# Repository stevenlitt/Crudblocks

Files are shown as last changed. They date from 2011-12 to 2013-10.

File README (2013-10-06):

Crudlabs Crudblocks

Arduino-based Modular Robotic Drum Controller

For a basic explanation of this project, please check out the Introduction to Crudblocks page on the wiki: https://github.com/stevenlitt/Crudblocks/wiki/Introduction-to-Crudblocks

All code, instructions, images, and other information and content 
provided strictly for non-commercial use.

Crudlabs + Crudblocks � Crudlabs 2012

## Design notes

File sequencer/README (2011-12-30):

Contains:

Arduino code (.pde)

Parts lists (.xls Excel spreadsheets)

3d printer files (.stl, .gcode, and .skp models designed in Google Sketchup)

PCB files (.sch, .brd, and gerbers)

where necessary for each sequencer module.

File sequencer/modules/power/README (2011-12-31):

Info on the power module and the recommended power supply coming early 2012.

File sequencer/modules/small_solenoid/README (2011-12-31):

This module uses the same Arduino code and PCBs as the "big_solenoid" module.

The parts list can also be found online as a Google Spreadsheet:

https://docs.google.com/spreadsheet/ccc?key=0AqVR8pqyuewQdG43TWpadEtsWEc4RVlPZjJQaXdpSFE

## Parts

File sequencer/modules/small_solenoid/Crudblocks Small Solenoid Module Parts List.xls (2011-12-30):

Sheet: Arduino on Breadboard
COMPONENT | QUANTITY | WHERE TO BUY | PART NUMBER | VENDOR PART NUMBER | ADDITIONAL COMMENTS | PRICE/UNIT | LINK
Multipurpose PC Board with 417 Holes | 1 | Radio Shack | 276-150 | 276-150 |  | 2.19 | http://www.radioshack.com/product/index.jsp?productId=2102845
Atmega328 with Arduino Bootloader | 1 | Sparkfun | DEV-10524 | DEV-10524 |  | 5.5 | http://www.sparkfun.com/products/10524
Violet LED | 1 | Sparkfun | COM-09851 | COM-09851 | in pack of 25 for $7.95 | 0.32 | http://www.sparkfun.com/products/9851
Standoff - Nylon (3/4", 4-40) | 4 | Sparkfun | PRT-10315 | PRT-10315 |  | 0.5 | http://www.sparkfun.com/products/10315
DIP Sockets Solder Tail - 28-Pin 0.3" | 1 | Sparkfun | PRT-07942 | PRT-07942 |  | 1.5 | http://www.sparkfun.com/products/7942
4-40 3/8" Screw | 8 | Mcmaster | 90279A108 | 90279A108 | in pack of 100 for $4.21. | 0.04 | http://www.mcmaster.com/#90279a108/=fb40lr
Mini Reset Switch | 1 | Mouser | B3F-1002 | 653-B3F-1002 |  | 0.24 | http://www.mouser.com/ProductDetail/Omron-Electronics/B3F-1002/
16MHz Clock Crystal | 1 | Mouser | ATS16A-E | 774-ATS16A-E |  | 0.54 | http://www.mouser.com/ProductDetail/CTS-Electronic-Components/ATS16A-E/
20pF Capacitor | 2 | Mouser | 140-100N2-200J-RC | 140-100N2-200J-RC | for clock | 0.08 | http://www.mouser.com/ProductDetail/Xicon/140-100N2-200J-RC/
10uF Capacitor | 1 | Sparkfun | COM-00523 | COM-00523 | between power and ground | 0.45 | http://www.sparkfun.com/products/523
10KOhm Resistor | 1 | Sparkfun | COM-08374 | COM-08374 | for reset switch | 0.25 | http://www.sparkfun.com/products/8374
330 Ohm Resistor | 1 | Sparkfun | COM-08377 | COM-08377 | for LED | 0.25 | http://www.sparkfun.com/products/8377
DIN5 Thru Hole Jack | 2 | Mouser | 161-0504-E | 161-0504-E |  | 0.98 | http://www.mouser.com/ProductDetail/Kobiconn/161-0504-E/?qs=xCMk%252bIHWTZMcaA%2fBF%2fgbrg%3d%3d

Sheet: Unique Parts
COMPONENT | QUANTITY | WHERE TO BUY | PART NUMBER | VENDOR PART NUMBER | ADDITIONAL COMMENTS | PRICE/UNIT | LINK
Solenoid | 1 | Lady Ada | 421 | 421 |  | 9.95 | http://www.adafruit.com/products/412
Screw Terminals 2.54mm Pitch (2-Pin) | 1 | Sparkfun | PRT-10571 | PRT-10571 |  | 0.75 | http://www.sparkfun.com/products/10571
4A Solid State Relay | 1 | Mouser | AQZ102 | 769-AQZ102 |  | 10.42 | http://www.mouser.com/ProductDetail/Panasonic-Electric-Works/AQZ102/
10KOhm Resistor | 1 | Sparkfun | COM-08374 | COM-08374 | for special command listener | 0.25 | http://www.sparkfun.com/products/8374
Mini Reset Switch | 1 | Mouser | B3F-1002 | 653-B3F-1002 | for special command listener | 0.24 | http://www.mouser.com/ProductDetail/Omron-Electronics/B3F-1002/
4-40 3/8" Screw | 8 | Mcmaster | 90279A108 | 90279A108 | in pack of 100 for $4.21. | 0.04 | http://www.mcmaster.com/#90279a108/=fb40lr

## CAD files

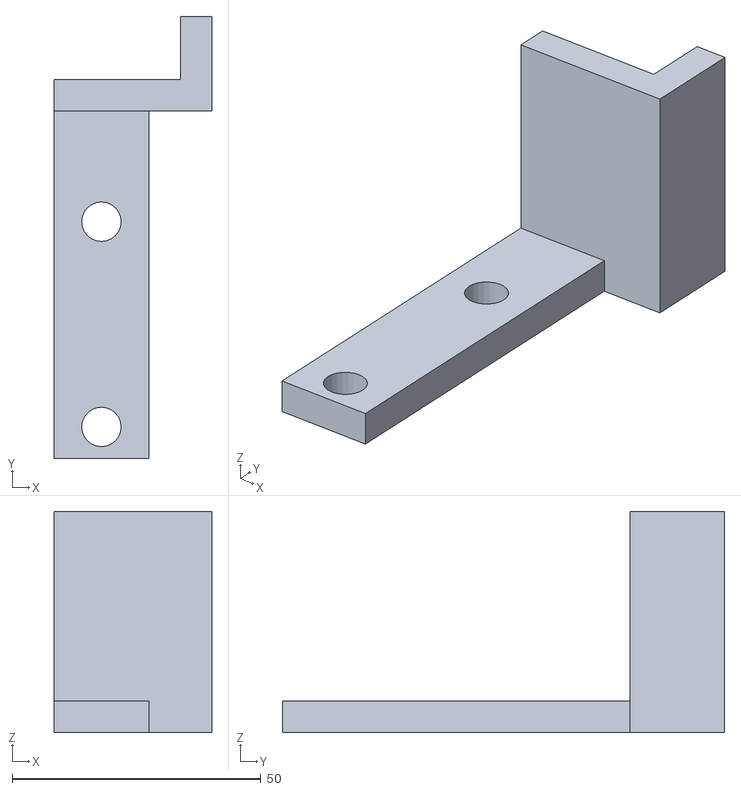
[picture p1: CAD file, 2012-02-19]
sequencer/modules/big_solenoid/makerbot/object_holder.stl
31.8 x 88.9 x 44.5

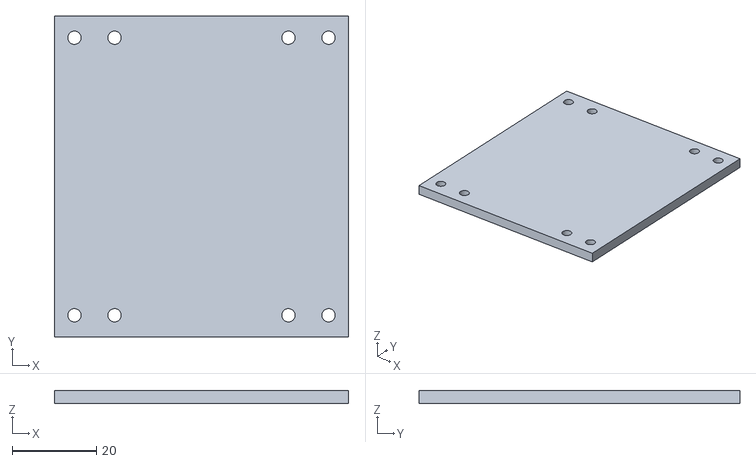
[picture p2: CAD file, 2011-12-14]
sequencer/modules/double_solenoid/makerbot/double_solenoid_electronics_connector_top.stl
69.8 x 76.2 x 3.18

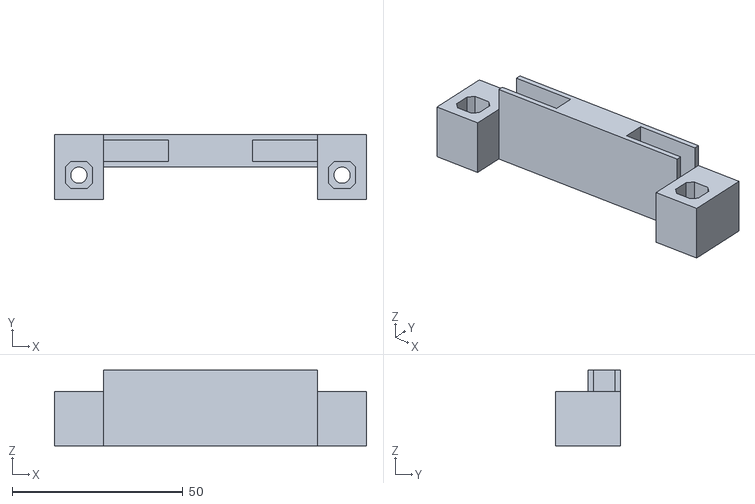
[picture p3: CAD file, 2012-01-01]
sequencer/modules/eight_step_sequencer/makerbot/double_standoff_joiner_with_magnet.stl
91.3 x 19.1 x 22.2

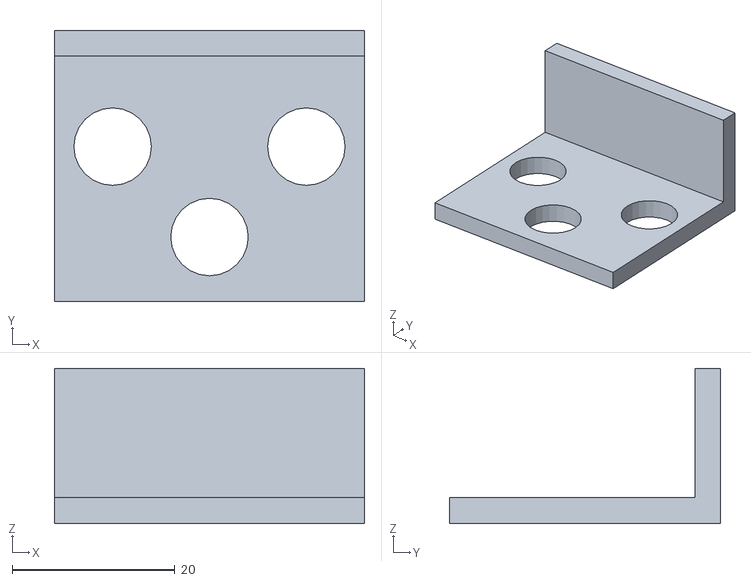
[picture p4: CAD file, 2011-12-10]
sequencer/modules/power/makerbot/power_module.stl
38.1 x 33.3 x 19.1

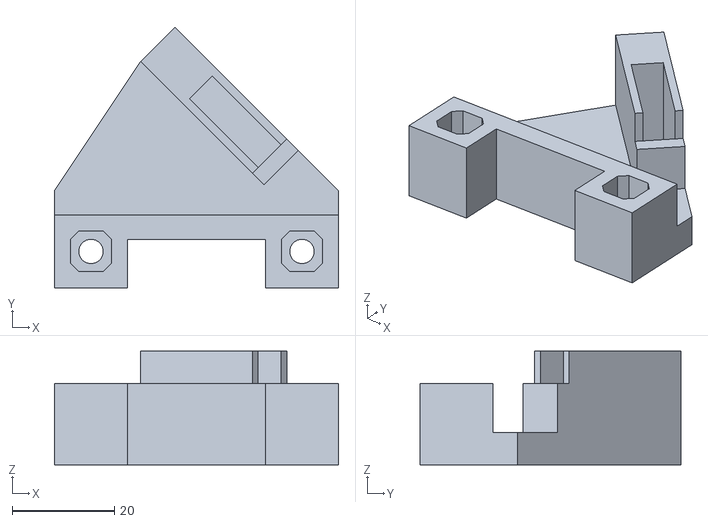
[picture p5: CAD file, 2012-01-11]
sequencer/modules/seven_seg_with_rot_encoder/makerbot/angled_standoff_joiner_with_magnet.stl
55.6 x 51.0 x 22.2

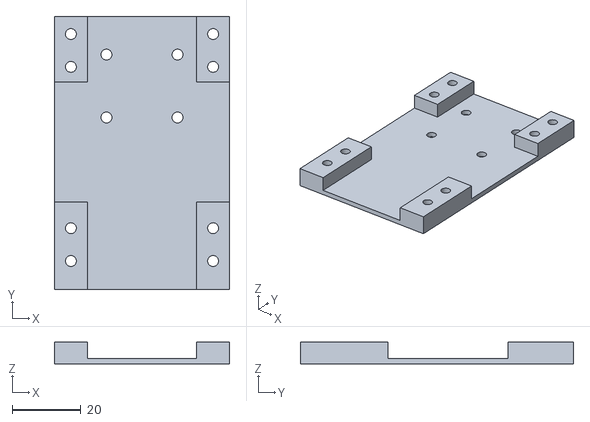
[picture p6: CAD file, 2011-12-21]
sequencer/modules/small_solenoid/makerbot/small_solenoid_electronics_connector.stl
50.8 x 79.4 x 6.35

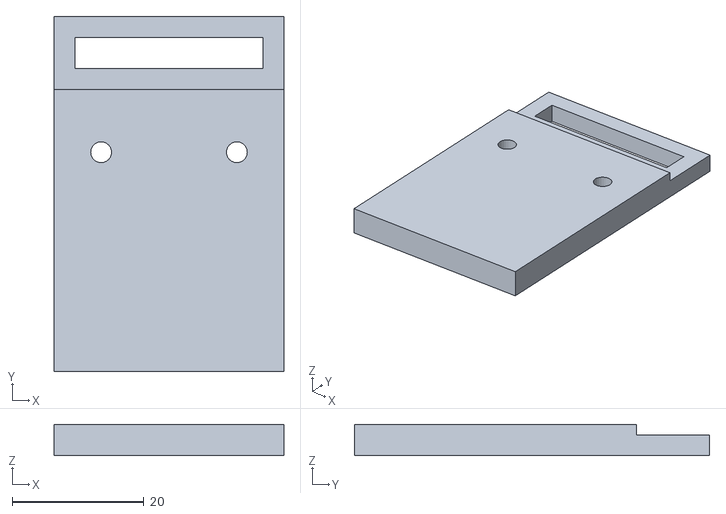
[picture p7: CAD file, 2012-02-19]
sequencer/modules/big_solenoid/makerbot/harness_longer.stl
34.9 x 54.0 x 4.76

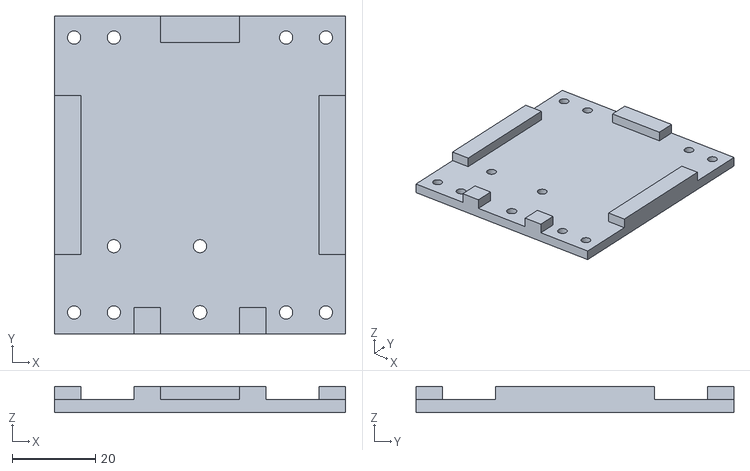
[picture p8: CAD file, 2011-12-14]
sequencer/modules/double_solenoid/makerbot/double_solenoid_electronics_connector_bottom.stl
69.8 x 76.2 x 6.35

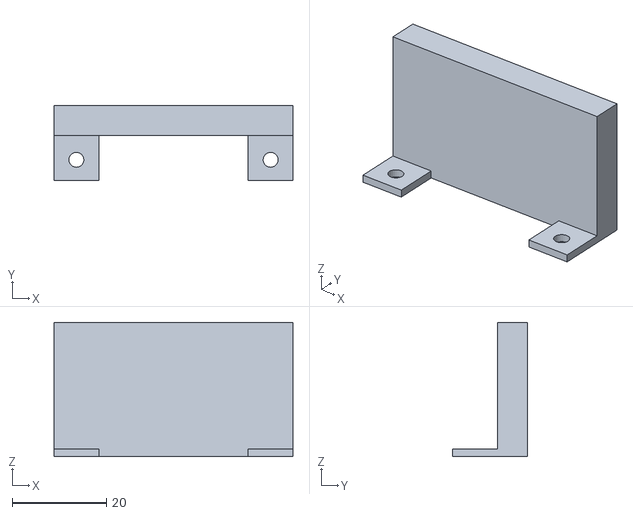
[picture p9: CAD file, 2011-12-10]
sequencer/modules/seven_seg_with_rot_encoder/makerbot/pcb_stand.stl
50.8 x 15.9 x 28.6

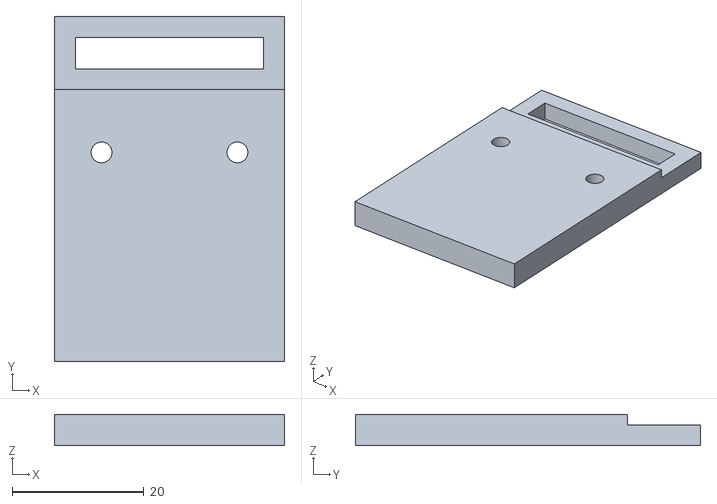
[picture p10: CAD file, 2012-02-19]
sequencer/modules/big_solenoid/makerbot/harness2.stl
34.9 x 52.4 x 4.76

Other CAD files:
sequencer/modules/big_solenoid/makerbot/harness2.skp
sequencer/modules/big_solenoid/makerbot/harness2~.skp
sequencer/modules/big_solenoid/makerbot/object_holder.skp
sequencer/modules/big_solenoid/makerbot/object_holder~.skp
sequencer/modules/double_solenoid/makerbot/double_solenoid_electronics_connector_bottom.skp
sequencer/modules/double_solenoid/makerbot/double_solenoid_electronics_connector_bottom~.skp
sequencer/modules/double_solenoid/makerbot/double_solenoid_electronics_connector_top.skp
sequencer/modules/eight_step_sequencer/makerbot/double_standoff_joiner_with_magnet.skp
sequencer/modules/eight_step_sequencer/makerbot/standoff_joiner_with_magnet.skp
sequencer/modules/eight_step_sequencer/makerbot/standoff_joiner_with_magnet~.skp
sequencer/modules/power/makerbot/power_module.skp
sequencer/modules/seven_seg_with_rot_encoder/makerbot/angled_standoff_joiner_with_magnet.skp
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

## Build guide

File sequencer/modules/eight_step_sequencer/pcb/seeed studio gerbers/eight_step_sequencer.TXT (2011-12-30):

%
M48
M72
T01C0.0240
T02C0.0276
T03C0.0300
T04C0.0320
T05C0.0400
T06C0.0520
T07C0.1250
%
T01
X8601Y14101
X17101Y16601
X21101Y19601
X26101Y20601
X26601Y21101
X35101Y16101
X35601Y10601
X31101Y7601
X27601Y4601
T02
X20101Y17601
X19101Y17601
X23101Y19601
X24101Y19601
X26101Y19601
X27101Y19601
T03
X29617Y17601
X31585Y17601
X31085Y10101
X29117Y10101
X26085Y10101
X24117Y10101
X21085Y10101
X19117Y10101
X16085Y10101
X14117Y10101
X11085Y10101
X9117Y10101
X6085Y10101
X4117Y10101
X4117Y5601
X6085Y5601
X9117Y5601
X11085Y5601
X14117Y5601
X16085Y5601
X19117Y5601
X21085Y5601
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

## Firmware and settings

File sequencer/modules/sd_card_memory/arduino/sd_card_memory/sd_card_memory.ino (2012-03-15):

/*----------------------------------------------------------------------
 
Crudlabs + Crudblocks Big Solenoid Module

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
 ----------------------------------------------------------------------*/
 

/*----------------------------------------------------------------------

   Sparkfun COM-09482 type 4 digit 7 segment display pinout diagram

                            16 15 14 13 12 11 10 9
                            ======================
                            |                    |
                            |8.  8.  :  8.  8.   |
                            |                    |
                            ======================
                            1  2  3  4  5  6  7  8


                  
                  AAAAAAA  AAAAAAA        AAAAAAA  AAAAAAA  
                  F     B  F     B        F     B  F     B  
                  F     B  F     B  COL   F     B  F     B  
                  F     B  F     B        F     B  F     B  
                  GGGGGGG  GGGGGGG        GGGGGGG  GGGGGGG  
                  E     C  E     C        E     C  E     C  
                  E     C  E     C  COL   E     C  E     C  
                  E     C  E     C        E     C  E     C  
                  DDDDDDD  DDDDDDD        DDDDDDD  DDDDDDD  



                          pin 1  =  digit 1 control
                          pin 2  =  digit 2 control
                          pin 6  =  digit 3 control
                          pin 8  =  digit 4 control
                          pin 3  =  LED D
                          pin 5  =  LED E
                          pin 11 =  LED F
                          pin 13 =  LED C
                          pin 14 =  LED A
                          pin 15 =  LED G
                          pin 16 =  LED B
  
----------------------------------------------------------------------*/

 
#include <SD.h>

#define channelSetterByte B11110001
#define next8Byte B11110011
#define switchChannelByte B11110010
#define setNumChannelsByte B11110100
#define setTempoByte B11110110
#define nextStepByte B11111001

#define BEGINLOADBYTE B11000001
#define LOADSTEPBYTE B11000010
#define ENDLOADBYTE B11000011
#define ENDCHANNELLOADBYTE B11000100

#define STARTSAVEBYTE B11000101
#define ENDSAVEBYTE B11000110
#define SAVEBITBYTE B11000111
#define SAVENEXTBYTE B11001000

//encoder stuff to delete after testing
#define SAVE_MODE 0
#define LOAD_MODE 1
#define numModes 2

int chipSelectPin = 2;
int ledLoadPin = 8;
int ledSavePin = 9;
int configPin = 7;

//encoder
int dpInEncoderA = A2;
int dpInEncoderB = A3;

//shift regs
int shiftOutLatchPin = 3;  //ST_CP of 74HC595
int shiftOutDataPin = 4;   //DS of 74HC595
int shiftOutClockPin = 5;  //SH_CP of 74HC595

//encoder
int encoderButtonPin = 6;
boolean encoderButtonValue = LOW;
boolean lastEncoderButtonValue = LOW;
int sevenSegDisplayMode = LOAD_MODE;
boolean showingWord = false;
unsigned long showingWordStartTime;
String wordToShow = "";
int encoderSubCount = 0;
int newEncoderPosition = 0;
int oldEncoderPosition = 0;

//7 seg
int digit1Address = 1;
int digit2Address = 1 << 1;
int digit3Address = 1 << 2;
int digit4Address = 1 << 3;

int currentPattern = 1;  //maybe need to change this name... ?  its the current pattern num displayed on the 7seg.... not the one playing on the sequencers

boolean lastConfigPinVal = LOW;

byte threeBytes[3] = {0, 0, 0};

boolean doMain = false;

unsigned long turnOnTime;
unsigned long preMainInterval = 3000;

File myFile;

String savedPattern = "";
String loadedPattern = "";

boolean sdInited = false;

boolean saving = false;
byte numChannelsSaved = 0;


void setup()
{
  Serial.begin(115200);
  pinMode(ledLoadPin, OUTPUT);  
  pinMode(ledSavePin, OUTPUT);
  
  pinMode(configPin, INPUT);
  
  //apparently we need to do this for the sd reader  
  pinMode(chipSelectPin, OUTPUT);  
  pinMode(10, OUTPUT);
  
  //for encoder
  pinMode(dpInEncoderA, INPUT);
  pinMode(dpInEncoderB, INPUT);  
  pinMode(encoderButtonPin,  INPUT);
  
  //for shiftregs
  pinMode(shiftOutLatchPin, OUTPUT);
  pinMode(shiftOutClockPin, OUTPUT);
  pinMode(shiftOutDataPin, OUTPUT);

  digitalWrite(dpInEncoderA, HIGH);
  digitalWrite(dpInEncoderB, HIGH);
  
  initSD();

  if(sdInited == true) initMode();
  
  turnOnTime = millis(); 
}

void loop() 
{
  goMain();  
}

void goMain() 
{
  checkConfigPin();  
  listenForSerial();
  readEncoder(); 
  checkEncoderSwitch();  
  draw7Seg();  
}

//CONFIG CONFIG CONFIG CONFIG CONFIG CONFIG CONFIG CONFIG CONFIG CONFIG CONFIG CONFIG CONFIG CONFIG CONFIG CONFIG CONFIG CONFIG CONFIG CONFIG CONFIG 
//CONFIG CONFIG CONFIG CONFIG CONFIG CONFIG CONFIG CONFIG CONFIG CONFIG CONFIG CONFIG CONFIG CONFIG CONFIG CONFIG CONFIG CONFIG CONFIG CONFIG CONFIG CONFIG 
//CONFIG CONFIG CONFIG CONFIG CONFIG CONFIG CONFIG CONFIG CONFIG CONFIG CONFIG CONFIG CONFIG CONFIG CONFIG CONFIG CONFIG CONFIG CONFIG CONFIG CONFIG 
//CONFIG CONFIG CONFIG CONFIG CONFIG CONFIG CONFIG CONFIG CONFIG CONFIG CONFIG CONFIG CONFIG CONFIG CONFIG CONFIG CONFIG CONFIG CONFIG CONFIG CONFIG CONFIG 
//CONFIG CONFIG CONFIG CONFIG CONFIG CONFIG CONFIG CONFIG CONFIG CONFIG CONFIG CONFIG CONFIG CONFIG CONFIG CONFIG CONFIG CONFIG CONFIG CONFIG CONFIG 

void checkConfigPin()
{  
  boolean val = digitalRead(configPin);
  
  if(val == HIGH && lastConfigPinVal == LOW)
  {
    if(sevenSegDisplayMode == SAVE_MODE) 
    {
      initSavePattern();
    }
    if(sevenSegDisplayMode == LOAD_MODE) 
    {
      loadSap();      
    }
  }
  
  lastConfigPinVal = val;
}


void sendOutPattern(String sap)
{
  writeThreeBytes( BEGINLOADBYTE, 0, 0 );
  
  for(int i = 0; i < sap.length(); i++)
  {
    if(sap.charAt(i) == '0') writeThreeBytes(LOADSTEPBYTE, 0, 0);
    else if(sap.charAt(i) == '1') writeThreeBytes(LOADSTEPBYTE, 1, 0);
    else if(sap.charAt(i) == ' ') writeThreeBytes(ENDCHANNELLOADBYTE, 0, 0);
  }

  writeThreeBytes(ENDLOADBYTE, 0, 0);
}

//ENCODER ENCODER ENCODER ENCODER ENCODER ENCODER ENCODER ENCODER ENCODER ENCODER ENCODER ENCODER ENCODER ENCODER ENCODER ENCODER ENCODER ENCODER ENCODER 
//ENCODER ENCODER ENCODER ENCODER ENCODER ENCODER ENCODER ENCODER ENCODER ENCODER ENCODER ENCODER ENCODER ENCODER ENCODER ENCODER ENCODER ENCODER ENCODER ENCODER 
//ENCODER ENCODER ENCODER ENCODER ENCODER ENCODER ENCODER ENCODER ENCODER ENCODER ENCODER ENCODER ENCODER ENCODER ENCODER ENCODER ENCODER ENCODER ENCODER 
//ENCODER ENCODER ENCODER ENCODER ENCODER ENCODER ENCODER ENCODER ENCODER ENCODER ENCODER ENCODER ENCODER ENCODER ENCODER ENCODER ENCODER ENCODER ENCODER ENCODER 
//ENCODER ENCODER ENCODER ENCODER ENCODER ENCODER ENCODER ENCODER ENCODER ENCODER ENCODER ENCODER ENCODER ENCODER ENCODER ENCODER ENCODER ENCODER ENCODER 


void checkEncoderSwitch()
{
  encoderButtonValue = digitalRead(encoderButtonPin);
  if(lastEncoderButtonValue == LOW && encoderButtonValue == HIGH)
  {
    changeMode();  
  }
  lastEncoderButtonValue = encoderButtonValue;
}

void readEncoder()
{  
  newEncoderPosition = (digitalRead(dpInEncoderB) * 2) + digitalRead(dpInEncoderA);

  if (newEncoderPosition != oldEncoderPosition)
  {
    
    // "Forward" is shown by the position going from (0 to 1) or (1 to 3)
    // or (3 to 2) or (2 to 0).  Anything else indicates that the user is
    // turning the device the other way.  Remember: this is Gray code, not
    // binary.
    int isFwd = ((oldEncoderPosition == 0) && (newEncoderPosition == 1)) ||
      ((oldEncoderPosition == 1) && (newEncoderPosition == 3)) ||
      ((oldEncoderPosition == 3) && (newEncoderPosition == 2)) ||
      ((oldEncoderPosition == 2) && (newEncoderPosition == 0));

    if (isFwd == true) encoderSubCount++;
    else if (isFwd == false) encoderSubCount--;
    
    //if we're looking at the mode name and we registered a turn... just hide the mode name... don't actually change the tempo, channel, etc value...
    if(showingWord == true && (encoderSubCount == -4 || encoderSubCount == 4)) {
      hideModeName();
      encoderSubCount = 0;
    //...otherwise change the value
    } else {
      if (encoderSubCount == -4)
      {
        if(sevenSegDisplayMode == SAVE_MODE) { 
          currentPattern++; 
          if(currentPattern > 99) currentPattern = 1;
        }
        else if(sevenSegDisplayMode == LOAD_MODE) { 
          currentPattern++;
          if(currentPattern > 99) currentPattern = 1;
        }
        encoderSubCount = 0;
      }
      else if (encoderSubCount == 4)
      {
        if(sevenSegDisplayMode == SAVE_MODE) { 
          currentPattern--; 
          if(currentPattern < 1) currentPattern = 99;
        }
        else if(sevenSegDisplayMode == LOAD_MODE) { 
          currentPattern--; 
          if(currentPattern < 1) currentPattern = 99;
        }
        encoderSubCount = 0;
      }
    }
    oldEncoderPosition = newEncoderPosition;    
  }
}

//BYTESTREAM BYTESTREAM BYTESTREAM BYTESTREAM BYTESTREAM BYTESTREAM BYTESTREAM BYTESTREAM BYTESTREAM BYTESTREAM BYTESTREAM BYTESTREAM BYTESTREAM 
//BYTESTREAM BYTESTREAM BYTESTREAM BYTESTREAM BYTESTREAM BYTESTREAM BYTESTREAM BYTESTREAM BYTESTREAM BYTESTREAM BYTESTREAM BYTESTREAM BYTESTREAM BYTESTREAM 
//BYTESTREAM BYTESTREAM BYTESTREAM BYTESTREAM BYTESTREAM BYTESTREAM BYTESTREAM BYTESTREAM BYTESTREAM BYTESTREAM BYTESTREAM BYTESTREAM BYTESTREAM 
//BYTESTREAM BYTESTREAM BYTESTREAM BYTESTREAM BYTESTREAM BYTESTREAM BYTESTREAM BYTESTREAM BYTESTREAM BYTESTREAM BYTESTREAM BYTESTREAM BYTESTREAM BYTESTREAM 
//BYTESTREAM BYTESTREAM BYTESTREAM BYTESTREAM BYTESTREAM BYTESTREAM BYTESTREAM BYTESTREAM BYTESTREAM BYTESTREAM BYTESTREAM BYTESTREAM BYTESTREAM 


void listenForSerial()
{  
  if(Serial.available() < 3) return;
  
  getThreeBytes();

  if(threeBytes[0] == BEGINLOADBYTE) return;
  if(threeBytes[0] == LOADSTEPBYTE) return;
  if(threeBytes[0] == ENDCHANNELLOADBYTE) return;
  if(threeBytes[0] == ENDLOADBYTE) { showWord("load"); return;  }
  if(threeBytes[0] == STARTSAVEBYTE) return;

  if(threeBytes[0] == SAVEBITBYTE)
  {
    byte b = threeBytes[1];
    savedPattern += String(b);
    return;
  }
  else if(threeBytes[0] == SAVENEXTBYTE)
  {
    savedPattern += ' ';
    numChannelsSaved++;
  }
  else if(threeBytes[0] == ENDSAVEBYTE)
  {
    showWord("save");     
    saveSap(); 
    saving = false;
    return;
  }
  
  sendOutThreeBytes();
  
}


void getThreeBytes()
{
  threeBytes[0] = Serial.read();
  threeBytes[1] = Serial.read();
  threeBytes[2] = Serial.read();
}


void sendOutThreeBytes()
{
  Serial.write(threeBytes[0]);
  Serial.write(threeBytes[1]);
  Serial.write(threeBytes[2]);  
}

void writeThreeBytes(byte b1, byte b2, byte b3)
{
  Serial.write(b1);
  Serial.write(b2);
  Serial.write(b3);
}

//SD SD SD SD SD SD SD SD SD SD SD SD SD SD SD SD SD SD SD SD SD SD SD SD SD SD SD SD SD SD SD SD SD SD SD SD SD SD SD SD SD SD SD SD SD SD SD SD SD 
//SD SD SD SD SD SD SD SD SD SD SD SD SD SD SD SD SD SD SD SD SD SD SD SD SD SD SD SD SD SD SD SD SD SD SD SD SD SD SD SD SD SD SD SD SD SD SD SD SD SD 
//SD SD SD SD SD SD SD SD SD SD SD SD SD SD SD SD SD SD SD SD SD SD SD SD SD SD SD SD SD SD SD SD SD SD SD SD SD SD SD SD SD SD SD SD SD SD SD SD SD 
//SD SD SD SD SD SD SD SD SD SD SD SD SD SD SD SD SD SD SD SD SD SD SD SD SD SD SD SD SD SD SD SD SD SD SD SD SD SD SD SD SD SD SD SD SD SD SD SD SD SD 
//SD SD SD SD SD SD SD SD SD SD SD SD SD SD SD SD SD SD SD SD SD SD SD SD SD SD SD SD SD SD SD SD SD SD SD SD SD SD SD SD SD SD SD SD SD SD SD SD SD 

void initSD()
{
  if (!SD.begin(chipSelectPin)) 
  {
    sdInited = false;    
    digitalWrite(ledLoadPin, HIGH);
    digitalWrite(ledSavePin, HIGH);
    return;
  } 
  else 
  {
    sdInited = true;  
  }
}


void saveSap()
{  
  String fileNameString = String(currentPattern) + ".SAP";
  char fileName[fileNameString.length() + 1];
  fileNameString.toCharArray(fileName, fileNameString.length() + 1);
//  File myFile = SD.open(fileName);
  
  if(SD.exists(fileName))
  {
  SD.remove(fileName);
  }
  myFile = SD.open(fileName, FILE_WRITE);
  myFile.println(savedPattern);
  myFile.close();  
}


void loadSap()
{
    loadedPattern = "";  
  
    String fileNameString = String(currentPattern) + ".SAP";
    char fileName[fileNameString.length() + 1];                              // why the + 1 ???
    fileNameString.toCharArray(fileName, fileNameString.length() + 1);       // here too??
    File myFile = SD.open(fileName);
    
    //if the file exists
    if(myFile == true)
    {
//      String newString = "";
      
      while(myFile.available())
      {
        //this is what you have to do to go from a byte to the proper char to a string... otherwise you can get the 0-255 as a String
        char c = myFile.read();
        String st = String(c);
        loadedPattern += st;
      }
      myFile.close();
      
      sendOutPattern(loadedPattern);
    }
}



void initSavePattern()
{  
  saving = true;
  numChannelsSaved = 0;  
  savedPattern = "";
  writeThreeBytes(STARTSAVEBYTE, 0, 0);
  writeThreeBytes(SAVENEXTBYTE, 0, 0);
}

//7SEG 7SEG 7SEG 7SEG 7SEG 7SEG 7SEG 7SEG 7SEG 7SEG 7SEG 7SEG 7SEG 7SEG 7SEG 7SEG 7SEG 7SEG 7SEG 7SEG 7SEG 7SEG 7SEG 7SEG
//7SEG 7SEG 7SEG 7SEG 7SEG 7SEG 7SEG 7SEG 7SEG 7SEG 7SEG 7SEG 7SEG 7SEG 7SEG 7SEG 7SEG 7SEG 7SEG 7SEG 7SEG 7SEG 7SEG 7SEG 7SEG
//7SEG 7SEG 7SEG 7SEG 7SEG 7SEG 7SEG 7SEG 7SEG 7SEG 7SEG 7SEG 7SEG 7SEG 7SEG 7SEG 7SEG 7SEG 7SEG 7SEG 7SEG 7SEG 7SEG 7SEG
//7SEG 7SEG 7SEG 7SEG 7SEG 7SEG 7SEG 7SEG 7SEG 7SEG 7SEG 7SEG 7SEG 7SEG 7SEG 7SEG 7SEG 7SEG 7SEG 7SEG 7SEG 7SEG 7SEG 7SEG 7SEG
//7SEG 7SEG 7SEG 7SEG 7SEG 7SEG 7SEG 7SEG 7SEG 7SEG 7SEG 7SEG 7SEG 7SEG 7SEG 7SEG 7SEG 7SEG 7SEG 7SEG 7SEG 7SEG 7SEG 7SEG


void draw7Seg() {
  
  if(showingWord == true && millis() > showingWordStartTime + 500)
  {
    showingWord = false;
  }
  
  if(showingWord == true) {
    
    displayWord(wordToShow);

  } else if(showingWord == false) {
  
    if(saving == true) displayNumber(savedPattern.length());
    else displayNumber(currentPattern);
/*
    {
    int numToDisplay;
    if(sevenSegDisplayMode == SAVE_MODE) numToDisplay = currentPattern;
    else if(sevenSegDisplayMode == LOAD_MODE) numToDisplay = currentPattern;
    }
*/       
  }
}

void displayNumber(int numToDisplay)
{
    byte digitToDisplay;
  
    digitToDisplay = (numToDisplay / 1000) % 10;
    setDigitToDisplay(1, digitToDisplay);
    
    digitToDisplay = (numToDisplay / 100) % 10;
    setDigitToDisplay(2, digitToDisplay);
    
    digitToDisplay = (numToDisplay / 10) % 10;
    setDigitToDisplay(3, digitToDisplay);
    
    digitToDisplay = numToDisplay % 10;
    setDigitToDisplay(4, digitToDisplay);  
}


void displayWord(String theWord)
{
  if(theWord == "tempo") {
    
    setLetterToDisplay(1, 't');
    setLetterToDisplay(2, 'e');
    setLetterToDisplay(3, 'm');
    setLetterToDisplay(4, 'p');
    
  } else if(theWord == "channel") {
    
    setLetterToDisplay(1, 'c');
    setLetterToDisplay(2, 'h');
    setLetterToDisplay(3, 'a');
    setLetterToDisplay(4, 'n');
    
  } else if(theWord == "pwm") {
    
    setLetterToDisplay(1, 'p');
    setLetterToDisplay(2, 'w');
    setLetterToDisplay(3, 'm');
    setLetterToDisplay(4, '_');
  }
  else if(theWord == "save")
  {
    setLetterToDisplay(1, 's');
    setLetterToDisplay(2, 'a');
    setLetterToDisplay(3, 'v');
    setLetterToDisplay(4, 'e');
  }
  else if(theWord == "load")
  {
    setLetterToDisplay(1, 'l');
    setLetterToDisplay(2, 'o');
    setLetterToDisplay(3, 'a');
    setLetterToDisplay(4, 'd');
  }  
}


void setLetterToDisplay(int ad, char letter) {
  
  byte letterAsByte = getLetterAsByte(letter);
  
  int address;
  if(ad == 1) address = digit1Address;
  else if(ad == 2) address = digit2Address;
  else if(ad == 3) address = digit3Address;
  else if(ad == 4) address = digit4Address;  
  
  digitalWrite(shiftOutLatchPin, LOW);
  shiftOut(shiftOutDataPin, shiftOutClockPin, MSBFIRST, letterAsByte);
  shiftOut(shiftOutDataPin, shiftOutClockPin, MSBFIRST, address);
  digitalWrite(shiftOutLatchPin, HIGH);    
}


void setDigitToDisplay(int ad, byte digit) {
  
  byte digitAsByte = getDigitAsByte(digit);
  
  int address;
  if(ad == 1) address = digit1Address;
  else if(ad == 2) address = digit2Address;
  else if(ad == 3) address = digit3Address;
  else if(ad == 4) address = digit4Address;
  
  digitalWrite(shiftOutLatchPin, LOW);
  shiftOut(shiftOutDataPin, shiftOutClockPin, MSBFIRST, digitAsByte);
  shiftOut(shiftOutDataPin, shiftOutClockPin, MSBFIRST, address);
  digitalWrite(shiftOutLatchPin, HIGH);  
}


void changeMode() {
    sevenSegDisplayMode++;
    if(sevenSegDisplayMode >= numModes) sevenSegDisplayMode = 0;    
    initMode();
}

void initMode()
{
  if(sevenSegDisplayMode == LOAD_MODE) showWord("load");
  else if(sevenSegDisplayMode == SAVE_MODE) showWord("save");  
  setModeLed();  
}

void showWord(String w)
{
  showingWordStartTime = millis();
  showingWord = true; 
  wordToShow = w;
}

void setModeLed() {
  if(sevenSegDisplayMode == SAVE_MODE)
  {
    digitalWrite(ledSavePin, HIGH);
    digitalWrite(ledLoadPin, LOW);    
  }
  else if(sevenSegDisplayMode == LOAD_MODE)
  {
    digitalWrite(ledSavePin, LOW);
    digitalWrite(ledLoadPin, HIGH);    
    
  }
}


void hideModeName() {
  showingWord = false;
}


byte getLetterAsByte(char letter)
{
  byte letterAsByte = 0;
  
  switch (letter) {

    case 'a':
    letterAsByte += 1 << 3;
    letterAsByte += 1 << 7;    
    break;    
    
    case 'c':
    letterAsByte += 1 << 1;
    letterAsByte += 1 << 2;
    letterAsByte += 1 << 6;
    letterAsByte += 1 << 7;    
    break;
    
    case 'd':
    letterAsByte += 1;
    letterAsByte += 1 << 5;
    letterAsByte += 1 << 7;
    break;    
    
    case 'e':
    letterAsByte += 1 << 1;
    letterAsByte += 1 << 2;
    letterAsByte += 1 << 7;    
    break;    

    case 'h':
    letterAsByte += 1;
    letterAsByte += 1 << 3;
    letterAsByte += 1 << 7;    
    break;

    case 'l':
    letterAsByte += 1;
    letterAsByte += 1 << 1;
    letterAsByte += 1 << 2;
    letterAsByte += 1 << 6;    
    letterAsByte += 1 << 7; 
    break;

    case 'm':
    letterAsByte += 1 << 4;
    letterAsByte += 1 << 5;
    letterAsByte += 1 << 7;    
    break;

    case 'n':
    letterAsByte += 1 << 3;
    letterAsByte += 1 << 6;  
    letterAsByte += 1 << 7;    
    break;

    case 'o':
    letterAsByte += 1 << 6;
    letterAsByte += 1 << 7;
    break;

    case 'p':
    letterAsByte += 1 << 2;
    letterAsByte += 1 << 3;
    letterAsByte += 1 << 7;    
    break;

    case 's':
    letterAsByte += 1 << 1;
    letterAsByte += 1 << 4;
    letterAsByte += 1 << 7;  
    break;
    
    case 't':
    letterAsByte += 1;
    letterAsByte += 1 << 1;
    letterAsByte += 1 << 2;
    letterAsByte += 1 << 7;    
    break;

    case 'v':
    letterAsByte += 1;
    letterAsByte += 1 << 6;
    letterAsByte += 1 << 7;
    break;  
   
    case 'w':
    letterAsByte += 1 << 4;
    letterAsByte += 1 << 5;
    letterAsByte += 1 << 7;    
    break;

    case '_':
    letterAsByte += 1;
    letterAsByte += 1 << 1;      
    letterAsByte += 1 << 2;  
    letterAsByte += 1 << 4;  
    letterAsByte += 1 << 5;
    letterAsByte += 1 << 6; 
    letterAsByte += 1 << 7;
    break;    
  }
  
  return letterAsByte;
}


byte getDigitAsByte(int digit)
{
  byte digitAsByte = 0;
  
  switch (digit) {

  case 0:
    digitAsByte += 1 << 6;
    digitAsByte += 1 << 7;    
    break;

  case 1:
    digitAsByte += 1;
    digitAsByte += 1 << 3;
    digitAsByte += 1 << 4;
    digitAsByte += 1 << 5;
    digitAsByte += 1 << 6;
    digitAsByte += 1 << 7;
    break;

  case 2:
    digitAsByte += 1 << 2;
    digitAsByte += 1 << 5;
    digitAsByte += 1 << 7;          
    break;

  case 3:
    digitAsByte += 1 << 4;
    digitAsByte += 1 << 5;
    digitAsByte += 1 << 7;              
    break;

  case 4:
    digitAsByte += 1;
    digitAsByte += 1 << 3;
    digitAsByte += 1 << 4;
    digitAsByte += 1 << 7;              
    break;

  case 5:
    digitAsByte += 1 << 1;
    digitAsByte += 1 << 4;
    digitAsByte += 1 << 7;              
    break;

  case 6:
    digitAsByte += 1 << 1;
    digitAsByte += 1 << 7;              
    break;

  case 7:
    digitAsByte += 1 << 3;
    digitAsByte += 1 << 4;
    digitAsByte += 1 << 5;
    digitAsByte += 1 << 6;
    digitAsByte += 1 << 7;              
    break;

  case 8:
//    digitAsByte = 0;
    digitAsByte += 1 << 7;              
    break;

  case 9:
    digitAsByte += 1 << 4;
    digitAsByte += 1 << 7;              
    break;
  }
  
  return digitAsByte;
}

void shiftOut(int myDataPin, int myClockPin, byte myDataOut) {
  int i=0;
  int pinState;
  pinMode(myClockPin, OUTPUT);
  pinMode(myDataPin, OUTPUT);

  digitalWrite(myDataPin, 0);
  digitalWrite(myClockPin, 0);

  for (i=7; i>=0; i--)  {
    digitalWrite(myClockPin, 0);
    if ( myDataOut & (1<<i) ) {
      pinState= 1;
    }
    else {	
      pinState= 0;
    }
    digitalWrite(myDataPin, pinState);
    digitalWrite(myClockPin, 1);
    digitalWrite(myDataPin, 0);
  }
  digitalWrite(myClockPin, 0);
}

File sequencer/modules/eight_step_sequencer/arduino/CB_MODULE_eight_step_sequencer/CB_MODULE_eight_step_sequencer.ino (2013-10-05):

/*----------------------------------------------------------------------
 
 Crudlabs + Crudblocks Eight Step Sequencer Module

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
---------------------------------------------------------------------*/
 
/*----------------------------------------------------------------------
 
 This code is for the controller sequencer.  It has 2 input shift registers for 16 steps,
 and 4 output shift registers, 2 for for 16 LEDs for the steps and 2 for a 4 digit 7 segment
 display.  The 6 seg display is controlled by a rotary encoder.  It sends MIDI messages out
 through serial.
 
---------------------------------------------------------------------*/


#define channelSetterByte B11110001
#define next8Byte B11110011
#define switchChannelByte B11110010
#define setNumChannelsByte B11110100
#define setTempoByte B11110110
#define nextStepByte B11111001

#define BEGINLOADBYTE B11000001
#define LOADSTEPBYTE B11000010
#define ENDLOADBYTE B11000011
#define ENDCHANNELLOADBYTE B11000100

#define STARTSAVEBYTE B11000101
#define ENDSAVEBYTE B11000110
#define SAVEBITBYTE B11000111
#define SAVENEXTBYTE B11001000

#define stepsOnArrayLength 256

int dpInEncoderA = A2;
int dpInEncoderB = A3;

int solenoidPin = A5;

int txPin = 2;
int rxPin = 3;

int setChannelsPin = 4;  //the button that launches config
boolean setChannelsPinValue = LOW;
boolean lastSetChannelsPinValue = LOW;

int encoderButtonPin = 5;
boolean encoderButtonValue = LOW;
boolean lastEncoderButtonValue = LOW;
int TEMPO_MODE = 0;
int CHANNEL_MODE = 1;
int sevenSegDisplayMode = TEMPO_MODE;

int shiftInClockPin = 7;  //yellow
int shiftInLatchPin = 8;  //green
int shiftInDataPin = 9;   //blue

int shiftOutLatchPin = 10;  //ST_CP of 74HC595, green
int shiftOutDataPin = 11;   //DS of 74HC595, blue
int shiftOutClockPin = 12;  //SH_CP of 74HC595, yellow

int shiftInByte1Array[8] = { 0, 0, 0, 0, 0, 0, 0, 0 };
int shiftInByte2Array[8] = { 0, 0, 0, 0, 0, 0, 0, 0 };
int lastShiftInByte1Array[8] = { 0, 0, 0, 0, 0, 0, 0, 0 };
int lastShiftInByte2Array[8] = { 0, 0, 0, 0, 0, 0, 0, 0 };


byte stepsOnArray[stepsOnArrayLength] = { 
  0, 0, 0, 0, 0, 0, 0, 0, 0, 0, 0, 0, 0, 0, 0, 0,
  0, 0, 0, 0, 0, 0, 0, 0, 0, 0, 0, 0, 0, 0, 0, 0,
  0, 0, 0, 0, 0, 0, 0, 0, 0, 0, 0, 0, 0, 0, 0, 0,
  0, 0, 0, 0, 0, 0, 0, 0, 0, 0, 0, 0, 0, 0, 0, 0,
  0, 0, 0, 0, 0, 0, 0, 0, 0, 0, 0, 0, 0, 0, 0, 0,
  0, 0, 0, 0, 0, 0, 0, 0, 0, 0, 0, 0, 0, 0, 0, 0,
  0, 0, 0, 0, 0, 0, 0, 0, 0, 0, 0, 0, 0, 0, 0, 0,
  0, 0, 0, 0, 0, 0, 0, 0, 0, 0, 0, 0, 0, 0, 0, 0,
  0, 0, 0, 0, 0, 0, 0, 0, 0, 0, 0, 0, 0, 0, 0, 0,
  0, 0, 0, 0, 0, 0, 0, 0, 0, 0, 0, 0, 0, 0, 0, 0,
  0, 0, 0, 0, 0, 0, 0, 0, 0, 0, 0, 0, 0, 0, 0, 0,
  0, 0, 0, 0, 0, 0, 0, 0, 0, 0, 0, 0, 0, 0, 0, 0,
  0, 0, 0, 0, 0, 0, 0, 0, 0, 0, 0, 0, 0, 0, 0, 0,
  0, 0, 0, 0, 0, 0, 0, 0, 0, 0, 0, 0, 0, 0, 0, 0,
  0, 0, 0, 0, 0, 0, 0, 0, 0, 0, 0, 0, 0, 0, 0, 0,
  0, 0, 0, 0, 0, 0, 0, 0, 0, 0, 0, 0, 0, 0, 0, 0
};

byte threeBytes[3] = { 0, 0, 0 };

byte shiftInByte1 = 0;
byte shiftInByte2 = 0;

byte shiftOutByte1 = 0;
byte shiftOutByte2 = 0;

unsigned long lastShift = 0;

int ledPin= 13;

int tempo = 120;
unsigned long lastStepTime = 0;
int currentStep = -1;
int totalSteps = 8;

int digit1Address = 1;
int digit2Address = 1 << 1;
int digit3Address = 1 << 2;
int digit4Address = 1 << 3;
byte digitAddressArray[4] = { digit1Address, digit2Address, digit3Address, digit4Address };

int encoderSubCount = 0;
int newEncoderPosition = 0;
int oldEncoderPosition = 0;

byte channel = 1;
byte channelOnNibble = (1 << 7) + (1 << 4);
byte channelOffNibble = 1 << 7;
byte numChannels = 16;

boolean initialNumChannelsSerialReceived = false;
boolean initialChannelsSetSerialReceived = false;

int serialDelay = 0;

boolean master = false;

boolean waitingForStep = false;
boolean justJumped = false;

boolean channelSwitchOn = false;

unsigned long turnOnTime = 0;
unsigned long preMainInterval = 3000;
boolean doMain = false;

int numSteps = 8;

boolean paused = false;

//helpers for load from sd card
int currentStepToWrite = 0;
int currentChannelToWrite = 0;
boolean memoryBytesLoaded = false;

//helpers for save to sd card
int channelToSave = 1;

unsigned long ledOnTime = 0;
unsigned long ledOnInterval = 0;

int stepEightPin = A2;

void setup() {
  Serial.begin(115200);

  pinMode(rxPin, INPUT);
  pinMode(txPin, OUTPUT);
  pinMode(setChannelsPin, INPUT);
  pinMode(dpInEncoderA, INPUT);
  pinMode(dpInEncoderB, INPUT);
  pinMode(encoderButtonPin, INPUT);
  pinMode(shiftOutLatchPin, OUTPUT);
  pinMode(shiftOutClockPin, OUTPUT);
  pinMode(shiftOutDataPin, OUTPUT);
  pinMode(shiftInLatchPin, OUTPUT);
  pinMode(shiftInClockPin, OUTPUT);
  pinMode(stepEightPin, OUTPUT);
  pinMode(shiftInDataPin, INPUT);
  pinMode(ledPin, OUTPUT);
  pinMode(solenoidPin, OUTPUT);

  digitalWrite(dpInEncoderA, HIGH);
  digitalWrite(dpInEncoderB, HIGH);
  digitalWrite(txPin, HIGH);

  turnOnTime = millis();
}


void loop() 
{
  if(doMain == false) preMain();
  else goMain();
}

void preMain() 
{
  while(Serial.available()) Serial.read();
  if(millis() > turnOnTime + preMainInterval) doMain = true;
}

void goMain() 
{
  if(initialNumChannelsSerialReceived == false)          //set output channels, etc
  {
    checkSetAddressPin();
    checkForSerialReceiveNumChannels();  
  }
  else if(initialChannelsSetSerialReceived == false)
  {
    checkForSerialReceiveChannelsSet();
  }
  else if(initialChannelsSetSerialReceived == true)      //...and start the sequencer once everything knows what and where it is
  {
    stepTempo();
    setLed();
    readInNextThreeBytes();
    shiftInAll();
    stepEightHack();
    shiftOutAll();
    checkChannelSwitch();
    checkSolenoid();
  }  
}

//INIT CONFIG INIT CONFIG  INIT CONFIG  INIT CONFIG  INIT CONFIG  INIT CONFIG  INIT CONFIG  INIT CONFIG  INIT CONFIG  INIT CONFIG  INIT CONFIG  INIT CONFIG 
//INIT CONFIG INIT CONFIG  INIT CONFIG  INIT CONFIG  INIT CONFIG  INIT CONFIG  INIT CONFIG  INIT CONFIG  INIT CONFIG  INIT CONFIG  INIT CONFIG  INIT CONFIG INIT CONFIG 
//INIT CONFIG INIT CONFIG  INIT CONFIG  INIT CONFIG  INIT CONFIG  INIT CONFIG  INIT CONFIG  INIT CONFIG  INIT CONFIG  INIT CONFIG  INIT CONFIG  INIT CONFIG 
//INIT CONFIG INIT CONFIG  INIT CONFIG  INIT CONFIG  INIT CONFIG  INIT CONFIG  INIT CONFIG  INIT CONFIG  INIT CONFIG  INIT CONFIG  INIT CONFIG  INIT CONFIG INIT CONFIG 
//INIT CONFIG INIT CONFIG  INIT CONFIG  INIT CONFIG  INIT CONFIG  INIT CONFIG  INIT CONFIG  INIT CONFIG  INIT CONFIG  INIT CONFIG  INIT CONFIG  INIT CONFIG
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

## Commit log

2011-12-10 added big_solenoid arduino code
2011-12-10 added eight_step_sequencer arduino code
2011-12-10 added seven_seg_with_rot_encoder arduino code
2011-12-10 added makerbot related files for big_solenoid module
    [solenoid_electronics_connector.skp, solenoid_electronics_connector.stl]
2011-12-10 re-added big_solenoid arduino code
2011-12-10 re-added eight_step_sequencer arduino code
2011-12-10 added makerbot related files for seven_seg_with_rot_encoder module
    [pcb_stand.skp, pcb_stand.stl]
2011-12-10 added sequencer power_supply dir and LOOKATME image
2011-12-10 rename power_module to power and add power makerbot files
    [power_module.skp, power_module.stl]
2011-12-11 added excel spreadsheets to sequencer parts lists
    [Crudblocks Big Solenoid Module Parts List.xls, Crudblocks Eight Step Sequencer Parts List.xls, Crudblocks Seven Seg with Rot Encoder Parts List.xls]
2011-12-12 added debug blink to eight_step Arduino code, improved big_relay Arduino code for config
2011-12-13 added double_solenoid module folder... code is good, 3d print files are not quite right and parts list isn't up yet
    [double_solenoid_electronics_connector.skp, double_solenoid_electronics_connector_bottom.stl, double_solenoid_electronics_connector~.skp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]
2011-12-14 double_solenoid module correct parts list and first decent makerbot design
    [Crudblocks Double Solenoid Module Parts List.xls, double_solenoid_electronics_connector.skp, double_solenoid_electronics_connector_bottom.stl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]
2011-12-14 new double_solenoid bottom print, all Serials changed from 9600 to 115200
    [double_solenoid_electronics_connector_bottom.skp, double_solenoid_electronics_connector_bottom.stl, double_solenoid_electronics_connector_bottom~.skp]
2011-12-14 new main readme with link to wiki
    [double_solenoid_electronics_connector_bottom.skp, double_solenoid_electronics_connector_bottom~.skp]
2011-12-14 correct makerbot designs for double_solenoid, no gcode yet since they haven't been printed
    [double_solenoid_electronics_connector_bottom.skp, double_solenoid_electronics_connector_bottom.stl, double_solenoid_electronics_connector_bottom~.skp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]
2011-12-14 better double_solenoid makerbot files
    [double_solenoid_electronics_connector_bottom.skp, double_solenoid_electronics_connector_bottom~.skp, double_solenoid_electronics_connector_top.stl]
2011-12-15 really good working pwm code for solenoid and double_solenoid
2011-12-19 extensive Arduino cleanup for all modules, fixed pause at step 1 on sequencer 1
    [CB_MODULE_big_relay.pde, CB_MODULE_double_solenoid.pde, CB_MODULE_eight_step_sequencer.pde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]
2011-12-21 small solenoid added, just 3d print files
    [small_solenoid_electronics_connector.skp, small_solenoid_electronics_connector.stl, small_solenoid_electronics_connector~.skp]
2011-12-22 config bugs seemingly fixed with 10 second delay on startup
    [CB_MODULE_big_relay.pde, CB_MODULE_double_solenoid.pde, CB_MODULE_eight_step_sequencer.pde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]
2011-12-27 first solenoid pcb
    [crudblocks_solenoid.brd, crudblocks_solenoid.sch]
2011-12-28 added 8step pcb
    [crudblocks_solenoid.brd, eight_step_sequencer.brd, eight_step_sequencer.sch]
2011-12-28 seven_seg pcb addded
    [crudblocks_solenoid.brd, crudblocks_solenoid.sch, seven_step_with_rot_encoder.brd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]
2011-12-29 added 10uf caps btw power and ground on all 3 pcbs
    [crudblocks_solenoid.brd, crudblocks_solenoid.sch, eight_step_sequencer.brd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]
2011-12-30 added small solenoid parts list, edited some READMEs
    [Crudblocks Small Solenoid Module Parts List.xls, crudblocks_solenoid.brd, crudblocks_solenoid.sch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]
2011-12-31 new readmes for double_solenoid, power, and small_solenoid
2012-01-01 3d printable joiners for sequencers added
    [double_standoff_joiner_with_magnet.skp, double_standoff_joiner_with_magnet.stl]
2012-01-01 3d print files for 7seg module
    [standoff_joiner_with_magnet.skp, standoff_joiner_with_magnet~.skp]
2012-01-01 added GPL to all Arduino code files
2012-01-11 first good Arduino code for midi in module
    [angled_standoff_joiner_with_magnet.skp, angled_standoff_joiner_with_magnet.stl, angled_standoff_joiner_with_magnet~.skp]
2012-01-19 Arduino codes updated for Arduino 1.0
2012-01-29 added empty arduino template
2012-01-31 added memory module with SD card Arduino code... with basics of sd breakout -> memory module -> ste sequencer communication working
2012-02-02 added 4x7seg and rotary encoder to sd_card_memory module
2012-02-05 added pcb + gerbers for sd card module
    [sd_card_memory.brd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]
2012-02-11 fixed sd card module init() problem (it was using the wrong chipselect pin)
    [crudblocks_solenoid.brd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]
2012-02-19 new 3d printed pieces for strapping velcro harnesses to sides of solenoids
    [harness2.skp, harness2.stl, harness2~.skp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]
2012-02-21 fixed SAVE actions so there's a 5 second delay between bit writes... which makes it work finally
    [CB_MODULE_eight_step_sequencer.ino, sd_card_memory.ino]
2012-04-22 added channel set to midi_in Arduino code
    [harness2.skp, harness2~.skp]
2012-04-27 midi in take one
    [midi_in.brd, midi_in.sch]
2012-04-27 capitalization cleanup
    [midi_in.sch]

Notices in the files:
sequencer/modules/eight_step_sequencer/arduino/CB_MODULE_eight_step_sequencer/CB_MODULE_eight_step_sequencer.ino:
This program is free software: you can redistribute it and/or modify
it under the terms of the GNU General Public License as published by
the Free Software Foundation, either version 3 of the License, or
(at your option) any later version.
